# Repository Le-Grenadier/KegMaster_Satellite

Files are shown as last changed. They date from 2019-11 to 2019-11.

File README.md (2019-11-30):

[EasyEDA Link to order PCB]|(https://easyeda.com/GrenardJ/kegmaster_satellitesmt)

Satellite PIC Application

Each PIC MCU manages hardware interface for a different keg. This includes GPIO to actuate valves, interrupt on change pins to data from the flow meter, logging and initiating ADC readings for the pressure sensor, reading data from the external HX711 24-bit ADC for the load-cell within the scale, and control output for the WS2812b LED driver. 

To improve overall system safety and security, a configurable dwell time is used to control how long a liquid or gas valve will remain open. This was implemented to help make the system resilient to loss of connection with the main controller and maintain security against attempts at physical intrusion. 
**Interface and Control Documentation**
* Each PIC shall have a base address of 0x08.
* Each PIC has two resistors, R20 and R22 on the PCB, to set the address offset. These shall be read as a two bit number (0-3) with R20 as the LSB.
* The following messages shall be defined for communication. If a response is indicated, the same format shall be used for both Tx and Rx. Pin Id’s may be found on the schematic within the Satellite PIC repository.

|Description|Message ID|(8-bit)Data Payload|Response|Notes|
|:--- |:---:|:--- |:--- |:--- |
|GPIO Read|0|Output Id (8-bit)\\State (8-bit)\\Hold Time (16-bit)||Yes||State and Hold time ignored on Rx.|
|GPIO Set|1|Output Id (8-bit)\\State (8-bit)\\Hold Time (16-bit)|No|
|GPIO Set Default|2|Output Id (8-bit)\\State (8-bit)\\Hold Time (16-bit)|No|Hold time is ignored.|
|Interrupt Read|3|Interrupt Id (8-bit)\\Count (16-bit)|Yes|Count ignored on Rx.|
|Interrupt Reset|4|Interrupt Id (8-bit)\\Count (16-bit)|No|Count ignored.|
|ADC Read|5|ADC Id (8-bit)\\Value (32-bit)|Yes|Value ignored on Rx.|
|LED Set Data|6|Led Cnt (8-bit)\\Led State[0..n]{\\ Red (8-bit)\\ Green (8-bit)\\ Blue (8-bit)\\ White (8-bit)\\}|No|LED State is a variable size array and can contain info for up to 20 LEDs. \\‘White’ ignored.|
|LED Set Breathe|7|State (8-bit)|No||

* Each message shall be terminated with the following 16-bit sequence 0x04FF. This was intended for the ability to send multiple messages in one transmission, however, this feature is untested. Messages without this terminator will be ignored.

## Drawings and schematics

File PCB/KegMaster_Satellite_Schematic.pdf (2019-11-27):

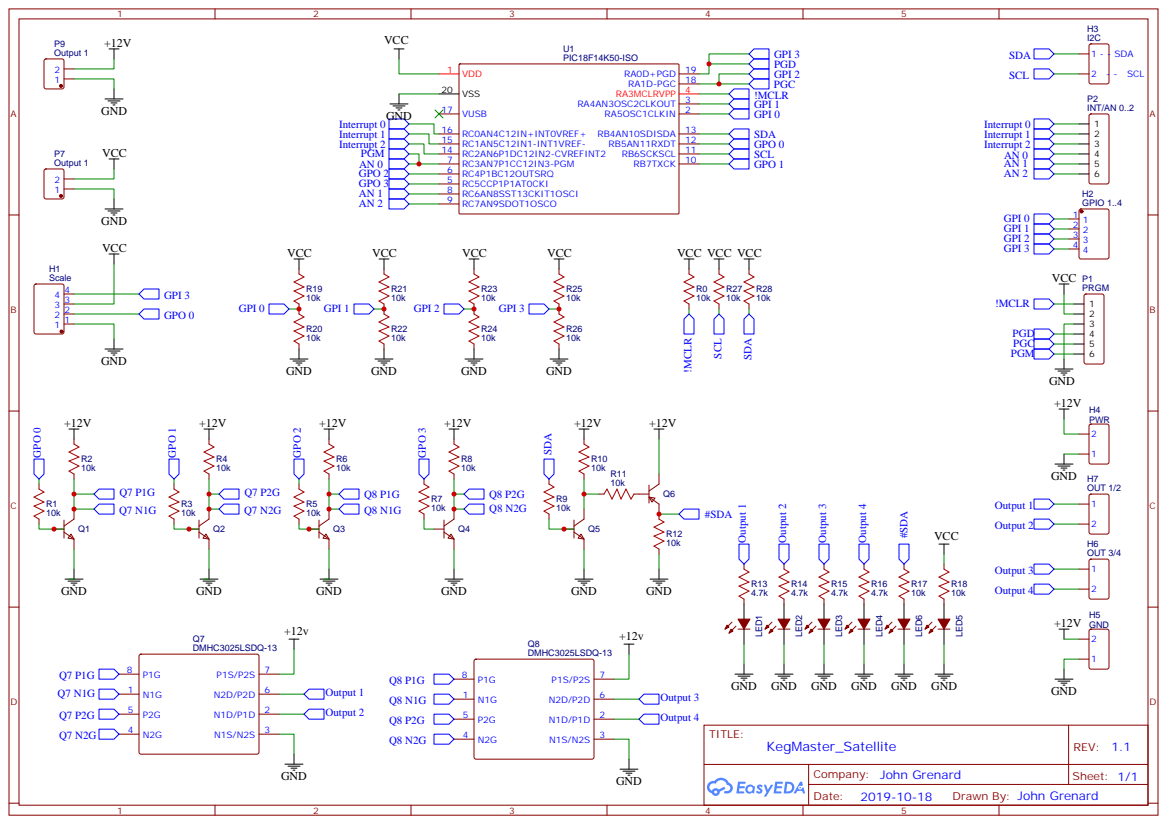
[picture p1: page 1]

GND GND

Drawn By: John Grenard

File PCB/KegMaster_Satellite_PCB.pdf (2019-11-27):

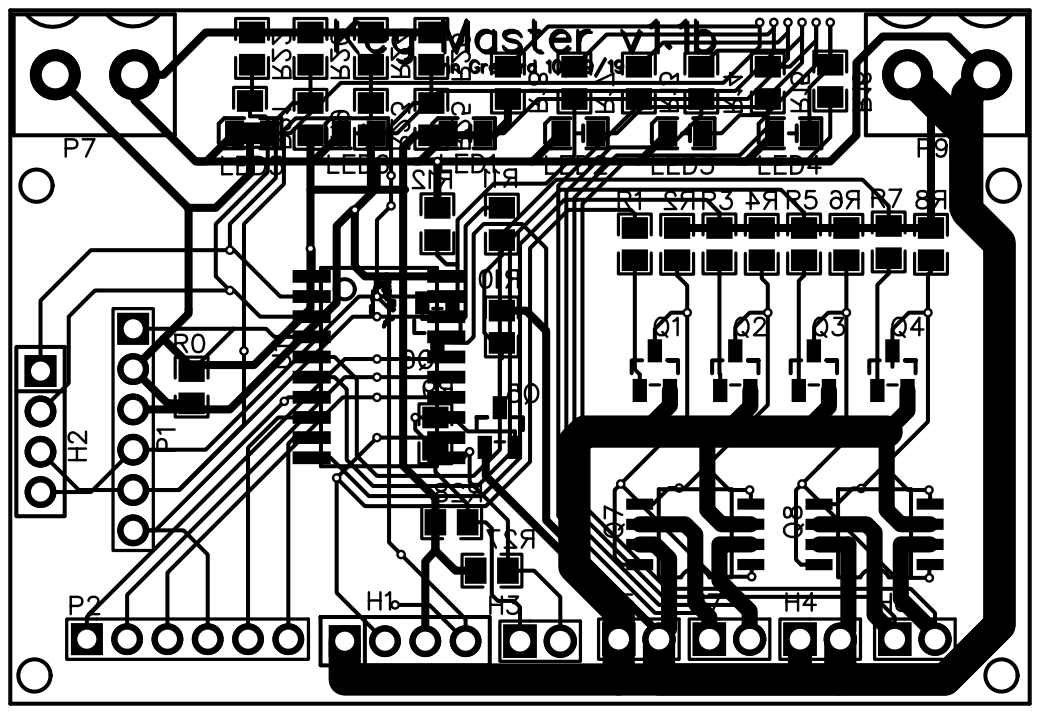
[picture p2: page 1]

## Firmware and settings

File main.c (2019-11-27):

/**
  Generated Main Source File

  Company:
    John Grenard
 
  File Name:
    main.c

  Summary:
    This is the main file generated using PIC10 / PIC12 / PIC16 / PIC18 MCUs

  Description:
    This header file provides implementations for driver APIs for all modules selected in the GUI.
    Generation Information :
        Product Revision  :  PIC10 / PIC12 / PIC16 / PIC18 MCUs - 1.77
        Device            :  PIC18F14K50
        Driver Version    :  2.00
*/

/*
    (c) 2018 Microchip Technology Inc. and its subsidiaries. 
    
    Subject to your compliance with these terms, you may use Microchip software and any 
    derivatives exclusively with Microchip products. It is your responsibility to comply with third party 
    license terms applicable to your use of third party software (including open source software) that 
    may accompany Microchip software.
    
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
    IN NO EVENT WILL MICROCHIP BE LIABLE FOR ANY INDIRECT, SPECIAL, PUNITIVE, 
    INCIDENTAL OR CONSEQUENTIAL LOSS, DAMAGE, COST OR EXPENSE OF ANY KIND 
    WHATSOEVER RELATED TO THE SOFTWARE, HOWEVER CAUSED, EVEN IF MICROCHIP 
    HAS BEEN ADVISED OF THE POSSIBILITY OR THE DAMAGES ARE FORESEEABLE. TO 
    THE FULLEST EXTENT ALLOWED BY LAW, MICROCHIP'S TOTAL LIABILITY ON ALL 
    CLAIMS IN ANY WAY RELATED TO THIS SOFTWARE WILL NOT EXCEED THE AMOUNT 
    OF FEES, IF ANY, THAT YOU HAVE PAID DIRECTLY TO MICROCHIP FOR THIS 
    SOFTWARE.
*/
#include <xc.h>
#include <stdbool.h>
#include <stdio.h>
#include <string.h>
#include "mcc.h"

#include "adc.h"
#include "adc_hx711.h"
#include "device_config.h"
#include "i2c_slave.h"
#include "interrupt_manager.h"
#include "led_ws2811.h"
#include "tsk_timer.h"
#include "ext_int.h"

#include "KegMaster_Satellite.h"
#include "gpio.h"

/*
Variables
*/
volatile uint24_t INT_count[] = {0,0,0};


/*
 Function Prototypes
 */
void Run(void);
void INT0_MyInterruptHandler(void);
void INT1_MyInterruptHandler(void);
void INT2_MyInterruptHandler(void);
void TMR0_MyInterruptHandler(void);
KegMaster_SatelliteMsgType* get_msg(void);
void expire_gpio(void);

/*
                         Main application
 */
void main(void)
{
    #define RANDOM_OFST 13
    static uint24_t timer_100ms = 0;
    static uint24_t timer_50ms = 0;
    static uint24_t timer_1ms = 0;
    uint24_t timeNow;
    
    // Initialize the device
    SYSTEM_Initialize();
    
    INT_Reset(0);
    INT0_SetInterruptHandler(INT0_MyInterruptHandler);
    
    INT_Reset(1);
    INT1_SetInterruptHandler(INT1_MyInterruptHandler);
    
    INT_Reset(2);
    INT2_SetInterruptHandler(INT2_MyInterruptHandler);

    /* init adc_hx711 */
    adc_hx711_init(&get_adc_hx711_data, &set_adc_hx711_clock);
    
    /* Init LED Driver */
    led_ws2811_init();
            
    /* I2C */
    i2c1_driver_open();
    i2c_slave_open();
    i2c1_driver_restart();
    i2c1_driver_start();
    mssp1_enableIRQ(); // Enable MSSP (I2C) Interrupts)
    
    /* Business Happens Here - Isochronous Data Processing for timing and stuff */
    TMR0_SetInterruptHandler(TMR0_MyInterruptHandler);
    TMR0_StartTimer();

    // If using interrupts in PIC18 High/Low Priority Mode you need to enable the Global High and Low Interrupts
    // If using interrupts in PIC Mid-Range Compatibility Mode you need to enable the Global and Peripheral Interrupts
    // Use the following macros to:

    // Enable the Global Interrupts
    INTERRUPT_GlobalInterruptEnable();

    // Disable the Global Interrupts
    //INTERRUPT_GlobalInterruptDisable();

    // Enable the Peripheral Interrupts
    INTERRUPT_PeripheralInterruptEnable();
    // Disable the Peripheral Interrupts
    //INTERRUPT_PeripheralInterruptDisable();
    while(1){
        timeNow = TSK_timer_get();
        if(timeNow > timer_100ms ){
            timer_100ms = TSK_timer_get() + 100;
            Run();
        }
        
        if(timeNow > (timer_50ms + RANDOM_OFST)){
            timer_50ms = TSK_timer_get() + 50;
            led_ws2811_rfsh();
        }
        
        if(timeNow > timer_1ms){
            timer_1ms = timeNow + 1;
            // Expire GPIO Dwell times
            gpio_outputDwellProc(timeNow);
        }
    }
}

void Run(void){   
    static uint8_t adc_id; 
    uint32_t scale = 0;
    
    if( ADC_IsConversionDone() ){
        adc_id += 1;
        adc_id %= (sizeof(adc_channels) / sizeof(adc_channels[0]));
        ADC_SelectChannel((adc_channel_t)adc_channels[adc_id]);
        ADC_StartConversion();
    }

    // Read HX711 ADC
    if( adc_hx711_read(&scale) )
    {
        adc_values[3] = scale;
    }
}

void INT0_MyInterruptHandler(void){
    static uint24_t tskTimePrev = 0;
    uint24_t tskTimeNow;
    
    /* Debounce Interrupts */
    tskTimeNow = TSK_timer_get();
    if( tskTimePrev == tskTimeNow ){
        return;
    }
    
    /* Low band filter */
    tskTimePrev = tskTimeNow;
    if((tskTimeNow - tskTimePrev) < 100){
        INT_count[0] = INT_count[0]+1;
    }
}

void INT1_MyInterruptHandler(void){
    static uint24_t tskTimePrev = 0;
    uint24_t tskTimeNow;
    
    /* Debounce Interrupts */
    tskTimeNow = TSK_timer_get();
    if( tskTimePrev == tskTimeNow ){
        return;
    }
    tskTimePrev = tskTimeNow;
    if((tskTimeNow - tskTimePrev) < 100){
        INT_count[1] = INT_count[1]+1;
    }
}

void INT2_MyInterruptHandler(void){
    static uint24_t tskTimePrev = 0;
    uint24_t tskTimeNow;
    
    /* Debounce Interrupts */
    tskTimeNow = TSK_timer_get();
    if( tskTimePrev == tskTimeNow ){
        return;
    }
    tskTimePrev = tskTimeNow;
    if((tskTimeNow - tskTimePrev) < 100){
        INT_count[2] = INT_count[2]+1;
    }
}

void TMR0_MyInterruptHandler(void){  
    TSK_timer++;
}

/**
 End of File
*/

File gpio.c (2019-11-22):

#include <assert.h>
#include <stdbool.h>
#include <string.h>

#include "mcc.h"
#include "pic18f14k50.h"

#include "gpio.h"
#include "pin_manager.h"
#include "tsk_timer.h"


/*==============================================================================
 * Literal Constants 
==============================================================================*/
/* Max of 20 because I'm feeling lazy and don't want to optimize atm */
#define MAX_IO 10
#define INPUT 1
#define OUTPUT 0
#define DWELL_TIME_DFLT 500


/*==============================================================================
 * Types 
==============================================================================*/
typedef struct{
    volatile unsigned char*  pinBus;
    uint8_t                  pinMask;
    volatile unsigned char*  tris;
    uint8_t                  trisMask;
} ioMap;


/*==============================================================================
 * Variables 
==============================================================================*/
uint8_t         inputPins_cnt;
const ioMap*    inputPins[MAX_IO];
uint8_t         outputPins_cnt;
const ioMap*    outputPins[MAX_IO];
bool            outputStateDflt[MAX_IO] = {0};
uint24_t        outputDwellTime[MAX_IO] = {DWELL_TIME_DFLT};
uint24_t        outputDwellTimer[MAX_IO] = {DWELL_TIME_DFLT};

/*==============================================================================
 * Memory Constants 
==============================================================================*/
static const ioMap inputMap[] = 
    {
    { &PORTA, _PORTA_RA0_MASK,  NULL,   0             },
    { &PORTA, _PORTA_RA1_MASK,  NULL,   0             },
    { &PORTA, _PORTA_RA3_MASK,  NULL,   0             },
    { &PORTA, _PORTA_RA4_MASK, &TRISA, _LATA_LA4_MASK },
    { &PORTA, _PORTA_RA5_MASK, &TRISA, _LATA_LA5_MASK },
										   
    { &PORTB, _PORTB_RB4_MASK, &TRISB, _LATB_LB4_MASK },
    { &PORTB, _PORTB_RB5_MASK, &TRISB, _LATB_LB5_MASK },
    { &PORTB, _PORTB_RB6_MASK, &TRISB, _LATB_LB6_MASK },
    { &PORTB, _PORTB_RB7_MASK, &TRISB, _LATB_LB7_MASK },
										   
    { &PORTC, _PORTC_RC0_MASK, &TRISC, _LATC_LC0_MASK },
    { &PORTC, _PORTC_RC1_MASK, &TRISC, _LATC_LC1_MASK },
    { &PORTC, _PORTC_RC2_MASK, &TRISC, _LATC_LC2_MASK },
    { &PORTC, _PORTC_RC3_MASK, &TRISC, _LATC_LC3_MASK },
    { &PORTC, _PORTC_RC4_MASK, &TRISC, _LATC_LC4_MASK },
    { &PORTC, _PORTC_RC5_MASK, &TRISC, _LATC_LC5_MASK },
    { &PORTC, _PORTC_RC6_MASK, &TRISC, _LATC_LC6_MASK },
    { &PORTC, _PORTC_RC7_MASK, &TRISC, _LATC_LC7_MASK },
};

static const ioMap outputMap[] =     
    {
    {  NULL,  0,               NULL,   0             },
    {  NULL,  0,               NULL,   0             },
    {  NULL,  0,               NULL,   0             },
    { &LATA, _LATA_LA4_MASK,  &TRISA, _LATA_LA4_MASK },
    { &LATA, _LATA_LA4_MASK,  &TRISA, _LATA_LA5_MASK },

    { &LATB, _LATB_LB4_MASK,  &TRISB, _LATB_LB4_MASK },
    { &LATB, _LATB_LB5_MASK,  &TRISB, _LATB_LB5_MASK },
    { &LATB, _LATB_LB6_MASK,  &TRISB, _LATB_LB6_MASK },
    { &LATB, _LATB_LB7_MASK,  &TRISB, _LATB_LB7_MASK },

    { &LATC, _LATC_LC0_MASK,  &TRISC, _LATC_LC0_MASK },
    { &LATC, _LATC_LC1_MASK,  &TRISC, _LATC_LC1_MASK },
    { &LATC, _LATC_LC2_MASK,  &TRISC, _LATC_LC2_MASK },
    { &LATC, _LATC_LC3_MASK,  &TRISC, _LATC_LC3_MASK },
    { &LATC, _LATC_LC4_MASK,  &TRISC, _LATC_LC4_MASK },
    { &LATC, _LATC_LC5_MASK,  &TRISC, _LATC_LC5_MASK },
    { &LATC, _LATC_LC6_MASK,  &TRISC, _LATC_LC6_MASK },
    { &LATC, _LATC_LC7_MASK,  &TRISC, _LATC_LC7_MASK },
    };

/*==============================================================================
 * Local Prototypes 
==============================================================================*/
static const ioMap* find_inputMap(volatile unsigned char*  pin, uint8_t mask);
static const ioMap* find_outputMap(volatile unsigned char* pin, uint8_t mask);
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

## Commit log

2019-09-09 Rough Wireframe of functionality - untested
2019-09-09 Initialize GPIO Hold Time - Fix Build Error
    [main.c]
2019-09-19 Fix Timer configuration and GPIO_Read
    [main.c]
2019-09-23 I2C Rx appears to be working
2019-09-23 Reset I2C interrupt after being serviced
2019-09-23 Read ADC in background
2019-09-23 Clean-up I2C message processing - WIP
2019-09-24 Fix problems with I2C Rx - WIP
    [main.c]
2019-09-25 I2C - Slave PIC now Acking address message
2019-09-28 I2C - Fix parts of input processing
    [main.c]
2019-09-28 I2C - Tx/Rx works. Needs clean-up
2019-09-28 I2C - now working along side ADC
2019-09-28 I2C - Pre-Initialize Rx buf pointer
2019-09-29 GPIO - Re-arch
    Output currently working
    Input needs work
2019-09-29 Timer - Fix 1ms Isochronous updates
    [main.c]
2019-09-29 Timer - Remove use of GPIO for debug
2019-10-02 Load Cell - ADC HX711 Initial driver implimentation (WIP)
2019-10-03 Add TSK timer functionality
2019-10-03 Timer - fix 1ms period (I suspect clk cnfg problem)
    [main.c]
2019-10-04 Scale - Data out via I2C works
    I'm not a huge fan of the current bit-banging code, but it works. Will improve later, maybe.
2019-10-06 GPIO - fix output driver setting whole bus
    [gpio.c, main.c]
2019-10-29 Update for new PCB
2019-11-01 Improve I2C robustness
2019-11-02 HX711 Load Cell - Fix GPIO mapping for scale input
    [gpio.c]
2019-11-04 I2C Driver - Fix memory leak
    [kegMaster.c]
2019-11-04 I2C Driver - Harden Tx ISR against potential errors
    [gpio.c]
2019-11-14 Add ability to set I2C addr with external resistors
2019-11-17 Remove RC3 (Analog idx 0) from being used as Low Volt Prog En Pin
2019-11-17 Meager attempt at handling Tsk Timer Overflows in GPIO Dwell Proc
    Tap 1 was/is having issues with CO2 En becoming stuck on after running overnight.
    [gpio.c, main.c]
2019-11-22 Add WS2812B (NeoPixel) LED driver
2019-11-23 Initial LED Driver - Control via I2C
2019-11-24 I2C Driver - Increase Rx buffer size to accommodate LED message data
    PIC is now out of memory
2019-11-27 Fix Interrupt filtering logic
    [main.c]
2019-11-27 Add PCB files
    [KegMaster_Satellite_Schematic_Altium_Format.schdoc]
